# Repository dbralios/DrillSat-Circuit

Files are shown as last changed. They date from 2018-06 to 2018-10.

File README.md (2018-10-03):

# White Noise

[White Noise](fb.com/WhiteNoiseGRE) is a space-engineering team from the National Technical University of Athens and currently consists of 6 members ( in alphabetical order ) :

* Dimitris Bralios 
* Chariton Charitonidis
* Iasonas Nikolaou
* Spyros Pavlatos
* George Rapakoulias
* Miltiadis Stouras

Our team won 1st prize in the [CanSat in Greece 2018](cansat.gr) competition.

# DrillSat

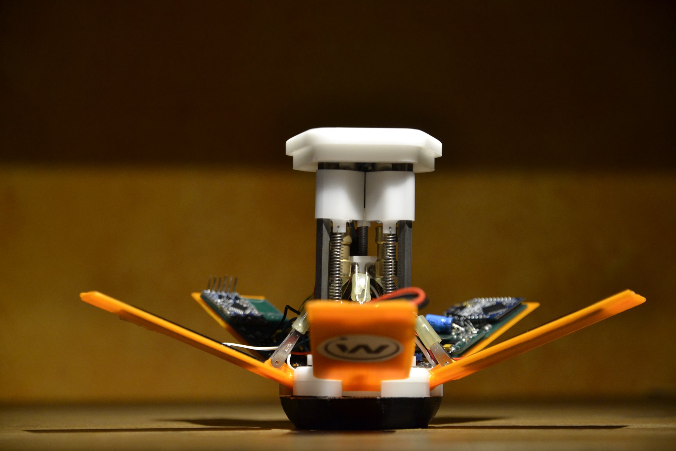
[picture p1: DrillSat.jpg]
DrillSat


Our goal was to develop a CanSat that can help in exploring new planets, as a part of our idea to use CubeSats in space exploration. Specifically, our CanSat, after a successful landing with the parachute, is able to use its [leg mechanism](https://www.youtube.com/watch?v=kTSUgSXn8OM) and rise into a position from which it can dig its drills to the ground and measure the soil's moisture with a sensor we developed.

# Electronics System 

The electronics system of the CanSat is comprised of an Arduino microcontroller, a UV sensor, a pressure and temperature sensor, a GPS, an XBee RF module, a conductivity sensor  and powered by a LiPo battery and four solar panels. The system apart from the battery the solar panels and the GPS, has to fit on top of two legs of the CanSat inside a space of 7x35x71mm. Due to that two PCBs were designed so the electronics can be mounted onto them. Also the structure has to be robust and survive any stresses, as well as operate continuously for 4 hours, constricting the power budget.

We have three boards on this repo. PCB1 connects an Arduino Pro Mini, an SD socket and a UV sensor (ML8511). PCB2 connects an XBee, the Solar Charger and a BMP sensor. The Solar Charger is a modified and shrunk version of the Adafruit board. 

PCB1 and PCB2 were designed on fritzing while the solar charger was designed on EAGLE.

## Sensor Subsystem

### Ultra Violet
The UV light sensor used is ML8511 mounted on a board. Equipped with an internal amplifier it converts the photo-diode current to voltage, outputing voltage linearly related to the UV light intensity measured in mW/cm2. The sensor output is stable across the operating temperature range, from -25C up to 75C, altough silght error is introduced away from the configuration temperature. Slight error is introduced by the temperature, although the operational temperature range is from -25C up to 75C. The spectral response is highest in the range 280 - 390nm which covers the UV-B spectrum and significant percentage of the UV-A spectrum. The typical supply current is around 300uA at the operational voltage of 3V.

### Pressure & Temperature
The sensor used to mesure temperature and barometric pressure is BMP280. The interface used to communicate with the microctroller is I2C. The pressure and temperature data, using the barometric formula, can give the current height with an accuracy of 1m. The operating pressure range is up to 9000m above sea level and from -40C to 85C regarding the temperature range, while the typical current draw is 2.7uA. 

### Conductivity Sensor

The conductivity sensor of the ground is implemented as a voltage divider. Two high speed steel drills are used space 18.2mm apart that penetrate 20mm in depth. One drill is connected to the ground voltage level while the other to +3.3V level through a 10KOhm resistor. Then the second drill is connected to an analogue pin of the microcontroller, as a result given the voltage at that pin and the resistance of the drills, we can specify the resistance between them.

### GPS

The GPS module used is the LEA-6H, which is mounted on the top of the CanSat. Typical supply current is 41mA and 47mA during the acquisition phase and the horizontal accuracy is 2.5m.

## Communication & Data Handling

### Microcontroller

The selected microcontroller board is the Arduino Pro Mini, using the ATmega328P, an 8-bit AVR microprocessor. It runs at 3.3V and 8MHz and has 14 input/output pins, 6 of them analog. The available program memory size is 32KByte, as well as 1024 Bytes of non volatile EEPROM memory, used to make the CanSat state-aware after possible power offs.

### RF Module

The RF module used for communication with the ground station is the XBee Pro S5 operating at 868MHz. It runs on 3.3 V consuming 60 mA at stand-by mode and 200 mA on packet emission and has a sensitivity of -112 dBm. It is used with an external antenna with 3 dBi gain. The same XBee module is also used on the ground station. The two modules are programmed to operate on AT Mode with ground station’s XBee being the coordinator and cansat’s XBee a router. Both modules transmit at a power of 25mW which is the legal local limit at 868MHz.

## Power Subsystem

A Polymer Lithium Ion battery, charged by four solar panels, is powering the CanSat. The battery has a voltage output of 3.7V and a capacity of 980mAh. Four 30.5mm by 58.5mm solar panels connected in serially, are used to charge the battery through the MCP73871. Then a low-dropout regulator drops the voltage down to 3.3V powering every piece of electronics, except for the GPS which has an onboard regulator and the the three motors.

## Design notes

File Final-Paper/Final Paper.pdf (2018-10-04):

## CFP-18-White-Noise

## CANSAT FINAL PAPER - DRILLSAT

### Authors Dimitris Bralios, bnbzor@gmail.com Chariton Charitonidis, haritoncharitonides@gmail.com Iasonas Nikolaou, iasonasnikolaou11@hotmail.com Spyros Pavlatos, spyrospavlatos4@gmail.com George Rapakoulias, george.rpk@outlook.com Miltiadis Stouras, m.stouras@gmail.com

Abstract: The CanSat in Greece competition aims at giving university students the opportunity to work on a multidisciplinary project with technology similar to that used in small satellites and to take their first steps in space. Moreover, the current trend in satellite technology which is to achieve more with a smaller probe, with prime examples being the CubeSats, makes this kind of competition more relevant. Our goal as a team was to design and build a CanSat that could be the basis for an actual space probe with the aim of extraterrestrial exploration. This paper presents our design of the CanSat discussing the mechanical, electrical and software aspects in detail, while showing that all the mission requirements are met. Specifically, our CanSat is launched onboard a research rocket and deployed at the apogee. Then a parachute is used to reach the nominal descent velocity. Equipped with five legs it is able to reach an upright position from where the drills can be activated. First, the leg and drill mechanisms are described in detail. Next, the selected sensors, the measurements taken and the electronics subsystem are discussed. Then, we present the flight software as well as the ground station that receives and visualizes the mission data in real time. Finally, we discuss the challenges we faced and draw conclusions.

CFP-18-White-Noise | Page 1 of 8

I. INTRODUCTION
The mission of our team for the 2018 CanSat in Greece competition consisted of the primary mission, same for all contestants, and the secondary one, selected by our team. In the primary mission we had to integrate sensors in our design, capable of measuring position, temperature and altitude during descent. The secondary mission was inspired from a number of real life projects in extraterrestrial exploration like the curiosity rover, the rosetta space probe, asteroid mining concepts etc. All those projects revolve around analysing the surface and soil of
planets | or | comets, | encountering | harsh
conditions. Our goal was to build a sensor for estimating soil moisture concentration and monitor it over time, in a supposed target planet, in order to further evaluate whether it could eventually host plants and support human activity. For further analysis, we added a UV sensor, since this is proven to be a key factor in the germination process.

II. PROJECT DESCRIPTION
The CanSat is launched onboard a Patriot type-rocket, with an apogee of 1 km where the probe is deployed. During the flight, a velocity of 500 km/h and an acceleration of 22 g could be reached. Next, throughout the descent the probe measures the barometric pressure, temperature and geographic coordinates. These measurements are stored as well as sent to the ground station in real time.
Requirements include the size of the probe, which has to fit inside a cylinder with a diameter of 65mm and a height of 115 mm. The descent rate after the deployment of the parachute should be in the range of 6 - 10 m/s. Also, the probe should be able to operate 4 hours continuously. Lastly, the mass of the CanSat should not exceed 350 grams.
Goal of the secondary mission is to measure the UV radiation and the soil moisture of the environment the CanSat is deployed in, from which we can exclude crucial information that can help us in our efforts to inhabit the target planet . After a successful landing with the parachute, it is able to use its leg mechanism and rise into a position from which it can dig its drills to the ground and measure the conductivity between the two drills, which is related to the moisture of the soil examined. Apart from the pressure and temperature sensor, a UV light sensor is added to determine if there is spectral content in the UV-A and UV-B range.
The data gathered are sent to the ground station, which is equipped with a high gain Yagi antenna with a range of 3 - 4 km. The frequency of the transmissions is 1 Hz. Through a web application the data received can be displayed and plotted in real time on a computer of the ground station.

III. MECHANICAL SYSTEM
In order to achieve our goals, a number of mechanisms had to be implemented in the design. The small size of the CanSat made it challenging to fit everything inside it in a robust way. After many prototypes, the following layout was chosen.

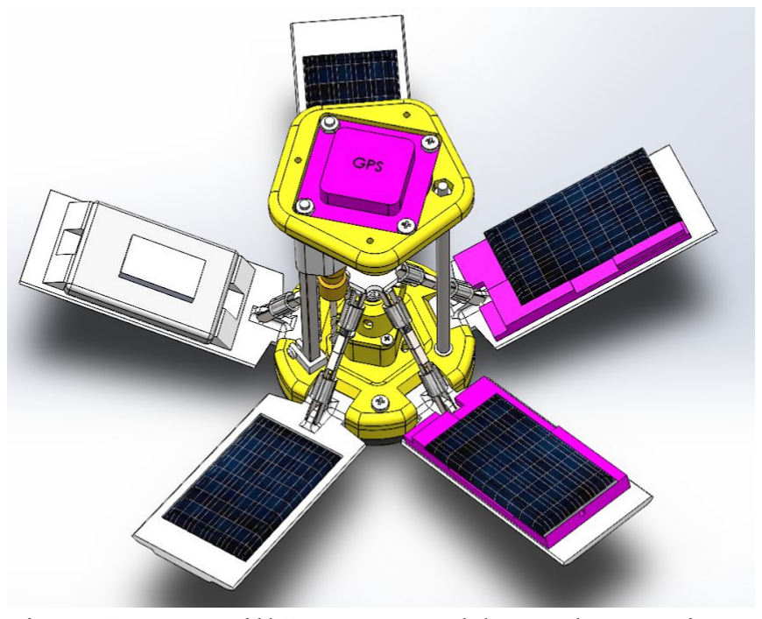
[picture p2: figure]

Fig. 1: DrillSat assembly, electronics represented with purple.

| All the electronics, the battery and the
solar panels were placed on the inside surface of the legs leaving space in the core of the CanSat for the drills and the leg deployment mechanism. A set of 5 foldable legs were placed in the periphery of the satellite, a number chosen to provide a good balance between leg width and near circular top view. A motor driven platform moving on a threaded rod, along with N clevis joints were used for deploying those legs. The length of each arm and the position of the joints were chosen carefully in order to give the mechanism an appropriate mechanical gain, allowing it to operate with a small motor and minimum current.

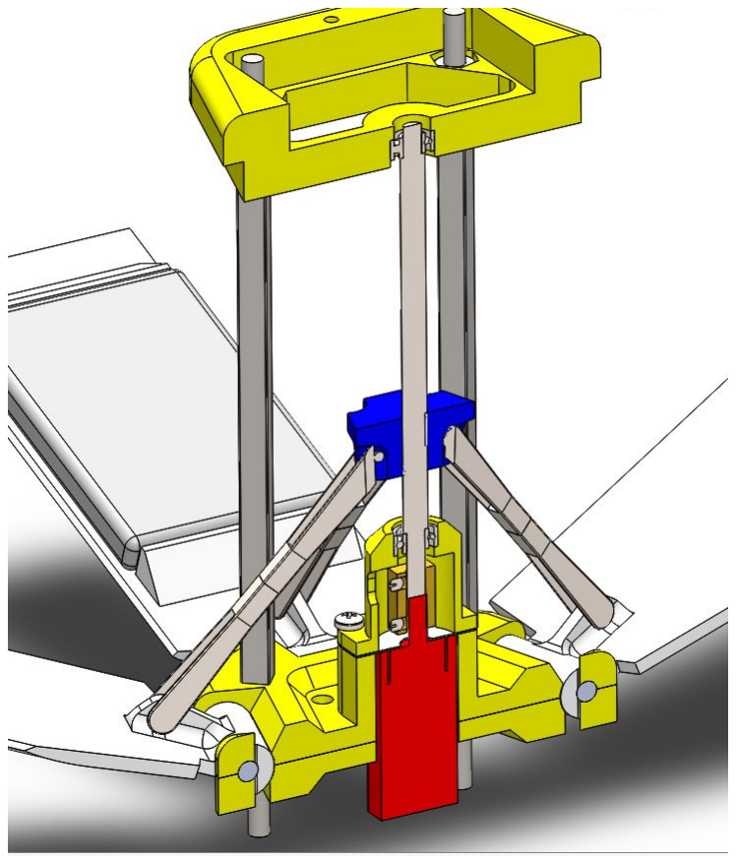
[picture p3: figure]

Fig. 2: Legs deployment mechanism

As for the drill mechanism, the drill assembly was sliding on a square 4x4 mm rod. In order to save space and weight, the assembly was moving with the aid of springs instead of actuators. An expendable retainer was used to prevent the drill from deploying. When voltage was applied to the motors, the drills would penetrate the retainer and protrude out of the CanSat, into the ground.

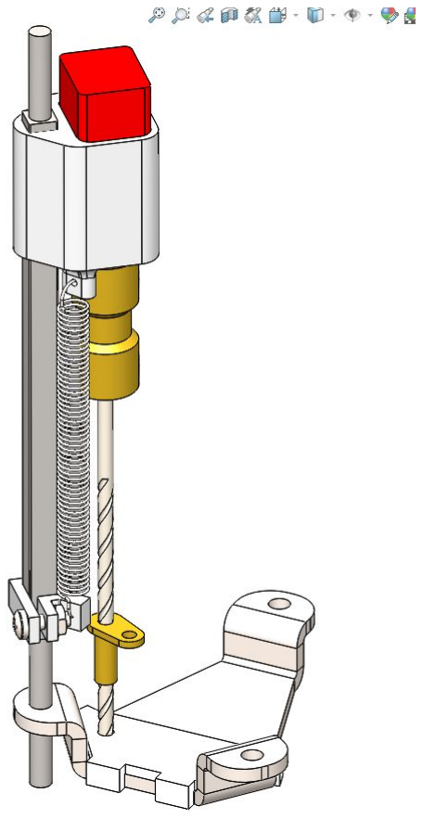
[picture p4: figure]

Fig. 3: Drill mechanism

Finally, in order to provide dampening in hard landings, some extra parts were added. A bottom made from TPC rubber was designed to make the first contact with the ground, absorbing most of the energy from the impact. Because the motor moving the legs was also located in the bottom of the satellite, we added a stainless steel metal cover around it.

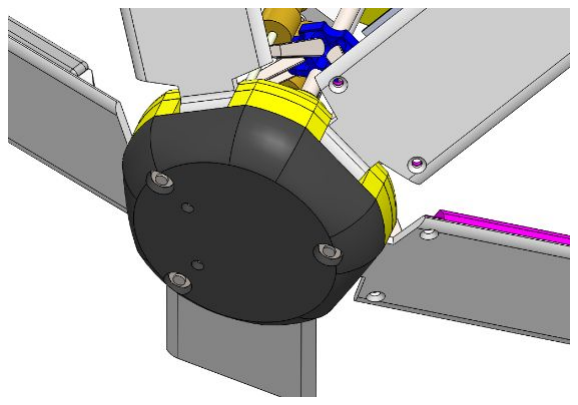
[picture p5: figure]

Fig. 4: Rubber damper

Most parts were CNC machined from POM plastic, ensuring high strength and dimensional precision. Metal parts were all made from stainless steel, with the exception of couplers, which were made from brass.
Apart from the satellite, we also constructed the parachute. We chose a classic circular design with a vent in the apex for stability. Its surface was first calculated theoretically using the following formula
F D = | [1]
2

CD

ρ V A

2

solved for A, given the terminal velocity (V), the total drag force (FD
), the air density (ρ) and the drag coefficient (CD

). After building the first prototype, fine-tuning was made in the surface area in order to achieve our target terminal velocity at 8 m/s, which we measured using image analysis from a video. Later on, for better precision, we also calculated the terminal velocity by conducting several drop tests in which we measured the height of the satellite in small constant time intervals and analyzed the measurements. The material we used was ripstop nylon. The diameter of the parachute was 48 cm and the diameter of the stability vent was 8 cm. A total of 8 buttonholes were made around the perimeter of the parachute fabric. A simple 2 mm kevlar thread was used for the suspension lines whose length was 50 cm enough to minimize the pitch of the CanSat.

IV. ELECTRONICS SYSTEM
The electronics system of the CanSat is comprised of an Arduino microcontroller, a UV sensor, a pressure and temperature sensor, a GPS, an XBee RF module anda conductivity sensor, all powered by a LiPo battery and four solar panels. The system apart from the battery the solar panels and the GPS, has to fit on top of two legs of the CanSat inside a space of 7x35x71 mm. Due to that two PCBs were designed so that the electronics can be mounted onto them. Also the structure had to be robust and survive any stresses, as well as being to run continuously for 4 hours, constricting the power budget.

IV.I. Sensor Subsystem
The UV light sensor used is ML8511 mounted on a board. Equipped with an internal amplifier it converts the photodiode current to voltage, outputting voltage linearly related to the UV light intensity measured in mW/cm

2
. The
sensor output is stable across the operating temperature range, from -25° C up to 75° C, although, when measuring in temperatures away from the one on which the sensor was calibrated, a slight error is introduced. The spectral response is highest in the range 280 - 390 nm which covers the UV-B spectrum and significant percentage of the UV-A spectrum. The typical supply current is around 300 μA at the operational voltage of 3 V.

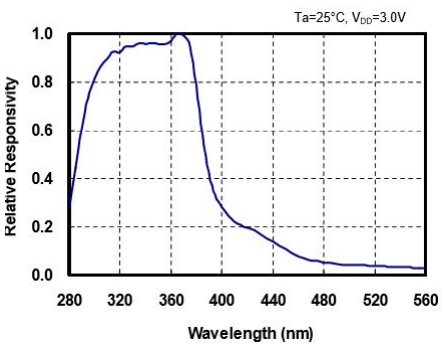
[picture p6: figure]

Fig. 5: Spectral response characteristics of ML8511

| The sensor used to measure temperature
and barometric pressure is BMP280. The interface used to communicate with the microcontroller is I2C. The pressure and temperature data, using the barometric formula, can give the current height with an accuracy of 1m. The operating pressure range is up to 9000 m above sea level and from -40° C to 85° C regarding the temperature range, while the typical current drawn is 2.7 μA.
The sensor used to measure the soil moisture is implemented as a voltage divider. Two high speed steel drills spaced 18.2mm apart are used to penetrate 20 mm in depth. One drill is connected to the ground voltage level through a 10K Ohm resistor while the other one to the +3.3 V level. The former drill is connected to an analog pin of the microcontroller. Given the voltage at that pin we can specify the resistance between them and then calculate the soil moisture.
The GPS module used is the LEA-6H, which is mounted on the top of the CanSat. It
sends | NAV-POSLLH | packages | to | the
microcontroller via serial connection, at a frequency of 1Hz. Typical supply current is 41 mA and 47 mA during the acquisition phase and the horizontal accuracy is 2.5 m.

IV.II. Communication and Data Handling The selected microcontroller board is the Arduino Pro Mini, using the ATmega328P, an 8-bit AVR microprocessor. It runs at 3.3 V and 8 MHz and has 14 input/output pins, 6 of them analog. The available program memory size is 32 KByte, as well as 1024 Bytes of non volatile EEPROM memory, used to make the CanSat state-aware after possible power offs. Apart from collecting and processing the measurements of the sensors the Arduino also controls the three motors through N-channel MOSFETS.
The RF module used for communication with the ground station is the XBee Pro S5 operating at 868MHz. It runs on 3.3 V consuming 60 mA at stand-by mode, 200 mA on packet emission and has a sensitivity of -112 dBm. It is used with an external antenna with 3 dBi gain which has the following radiation pattern.

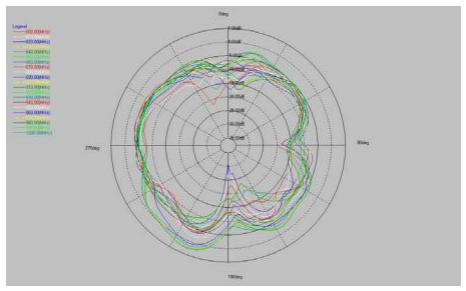
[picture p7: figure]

Fig. 6: Radiation pattern of the probe’s antenna

The same XBee module is also used on the ground station. The two modules are programmed to operate on AT Mode with ground station’s XBee being the coordinator and cansat’s XBee a router. Both modules transmit at a power of 25mW which is the legal local limit at 868MHz.

IV.III. Electrical Power Subsystem
A Polymer Lithium Ion battery, charged by four solar panels, is powering the CanSat. The battery has a voltage output of 3.7 V and a capacity of 980 mAh. Four 30.5 mm by 58.5 mm solar panels connected serially are used to charge the battery through the MCP73871. Then a low-dropout regulator drops the voltage down to 3.3 V powering every piece of electronics, except for the GPS, which has an onboard regulator, and the three motors.

Voltage
(V)

Current
(mA)

Power
(mW)
Arduino | 3.3 | 25 | 82.5
XBee | 3.3 | 60 | 198
GPS | 3.7 | 50 | 165
SD card | 3.3 | 30 | 99
BMP sensor 3.3 | 1 | 3.3
UV sensor | 3.3 | 0.5 | 1.65
Motors | 3.7 | 350 | 1295
Table 1: Power budget
Through experiments the previous values of current drawn were found. We conclude that the battery selected is able to power the CanSat for the required time duration.
V. FLIGHT SOFTWARE
The flight software consists of three software states: Launching, Descent and Ground Operations. In each state, the sequence of events is:
1. Take measurements
2. Save measurements to SD Card
3. Send a telemetry package containing the last measurements to ground station
4. Process data and determine the new software state

To ensure that our mission’s state is maintained through unexpected processor resets, some information regarding the current state is stored on the non-volatile memory (EEPROM) of the microcontroller, so it can be queried on processor start-up. Being able to dynamically determine our software state is vital for the success of the flight software because a simple sequential program could get stuck in the wrong software state after a sudden reset and lose control of the mission. The flight software is visualised in the flowchart of Fig. 7.

VI. GROUND CONTROL SYSTEM
The ground station consists of a personal computer, an Xbee Pro S5 and a Yagi Antenna with 8 dBi gain. The Xbee is connected via USB to the computer, and the Yagi Antenna is attached to the Xbee module with an RP-SMA connector. The data received by the computer, is parsed by a python script, checked for errors, and saved in a JSON format. Meanwhile a node.js server running locally serves a web page where the data is plotted in real-time using React.js and plotly.js.

VII. CONCLUSION
If we were to rebuild the satellite, we would have made a number of changes, both in the mechanisms and the circuits. One thing we found particularly hard was integrating all cables in the design. Lack of space along with the fact that the circuit boards were in moving parts of the cansat made this even harder. Using cable ribbons and socket connectors would give better results as well. Furthermore, a future upgrade would be the design of PCBs that host most of the electronics components, the sensors themselves and not serving as connectors between various sensor boards. Lastly, another minor enhancement would be to establish a 2-way communication with the satellite, changing the antennas’ and the software accordingly, in order to be able to query the satellite for values that are typically not included in mission’s telemetry packages (i.e. values stored in EEPROM), as well as have it to execute orders given from the ground station in real-time.
In conclusion, with the end of this project, our team has gained significant knowledge and experience. We believe that by constructing DrillSat we have proved our initial standing, that CanSats and CubeSats can include complex mechanisms and be used in a wide variety of space missions (such as extraterrestrial exploration) .

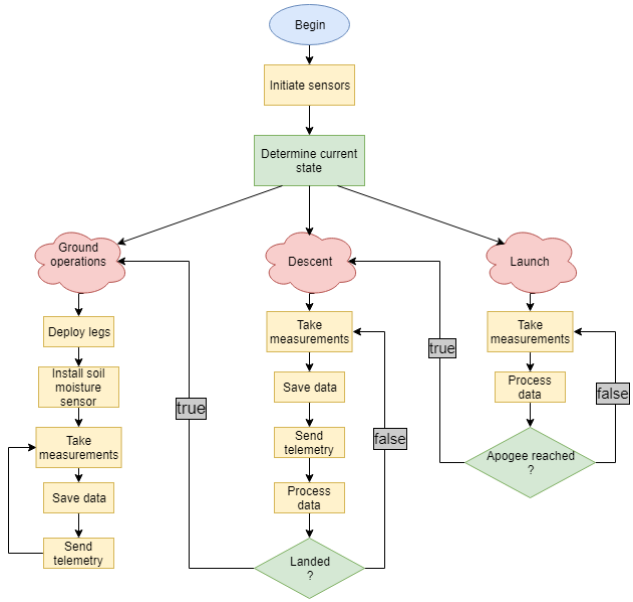
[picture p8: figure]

Fig. 7: Flight software flowchart

VII. REFERENCES
-CanSat in Greece portal: www.cansat.gr -Christos Papadopoulos, Machine Design, 3rd edition 2017
-UV Sensor with Voltage Output. ML8511. Rev. 5.0. Lapis Semiconductor. Mar. 2013.
-Digital Pressure Sensor. BMP280. Rev. 1.14. Bosch Sensortec. Mar. 2015.
-LEA-6 u-blox 6 GPS Modules. UBX-14044797. Rev. 13.0. U-blox. Feb. 2017.
-8-bit | AVR | Microcontrollers.
Atmel-42735B-ATmega328/P. Rev. B. Atmel. Nov. 2016.
-XBee-PRO 868 RF Module. Rev. F. Digi International. May. 2015.
-Polymer Lithium-Ion Battery. LP573450. Rev. 1.0. Cellevia Batteries. May. 2017.
-Stand-Alone | System | Load | Sharing | and
Li-Ion/Li-Polymer Battery Charge Management Controller. MCP73871. Rev. C. Microchip Technology. Sep. 2013.
-Arduino Documentation: www.arduino.cc

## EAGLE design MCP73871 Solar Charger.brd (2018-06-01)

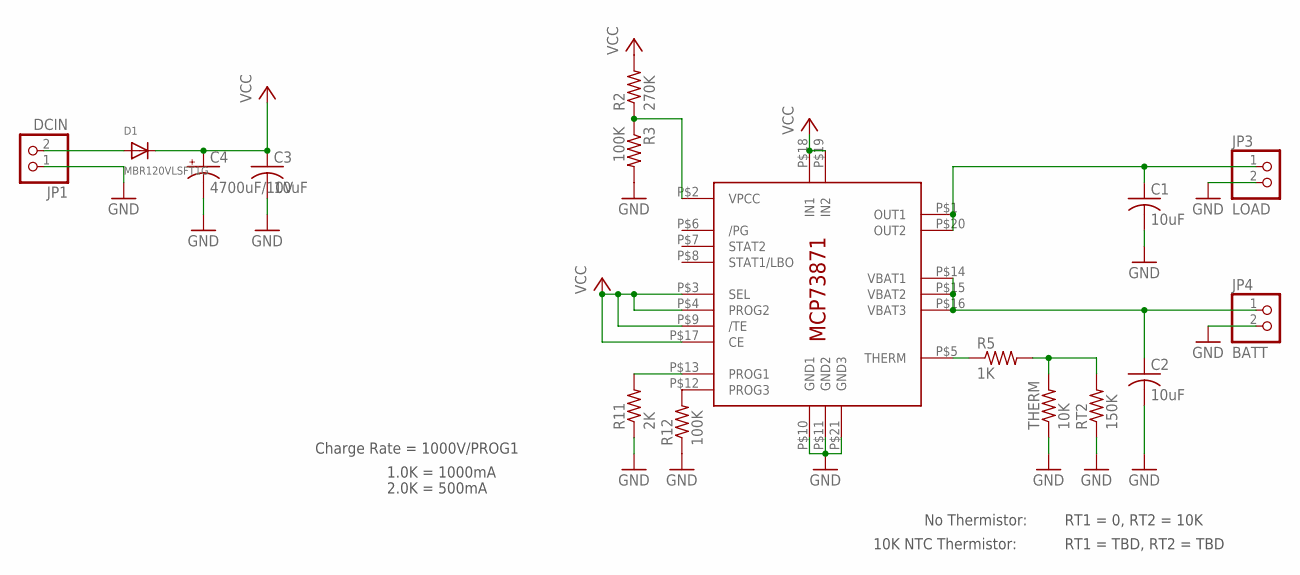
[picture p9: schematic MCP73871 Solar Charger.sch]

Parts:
C1, C2, C3: 10uF; C0805K
C4: 4700uF/10V; E5-10,5
D1: MBR120VLSFT1G; SOD-123
IC1: MCP73871; QFN20_4MM
JP1: DCIN; 1X02_OVAL
JP3: LOAD; 1X02_ROUND
JP4: BATT; 1X02_ROUND
R2: 270K; R0805
R3, R12: 100K; R0805
R5: 1K; M0805
R11: 2K; M0805
RT2: 150K; M0805
THERM: 10K; M0805

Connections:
BATT: C2.1, IC1.P$14 (VBAT1), IC1.P$15 (VBAT2), IC1.P$16 (VBAT3), JP4.1
GND: C1.2, C2.2, C3.2, C4.-, IC1.P$10 (GND1), IC1.P$11 (GND2), IC1.P$21 (GND3), JP1.1, JP3.2, JP4.2, R3.2, R11.1, R12.1, RT2.1, THERM.1
unnamed: D1.A, JP1.2
unnamed: IC1.P$5 (THERM), R5.1
unnamed: IC1.P$2 (VPCC), R2.1, R3.1
unnamed: R5.2, RT2.2, THERM.2
unnamed: IC1.P$12 (PROG3), R12.2
unnamed: IC1.P$13 (PROG1), R11.2
OUT: C1.1, IC1.P$1 (OUT1), IC1.P$20 (OUT2), JP3.1
VCC: C3.1, C4.+, D1.C, IC1.P$3 (SEL), IC1.P$4 (PROG2), IC1.P$9 (/TE), IC1.P$17 (CE), IC1.P$18 (IN1), IC1.P$19 (IN2), R2.2

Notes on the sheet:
Charge Rate = 1000V/PROG1
1.0K = 1000mA
2.0K = 500mA
No Thermistor:
10K NTC Thermistor:
RT1 = 0, RT2 = 10K
RT1 = TBD, RT2 = TBD

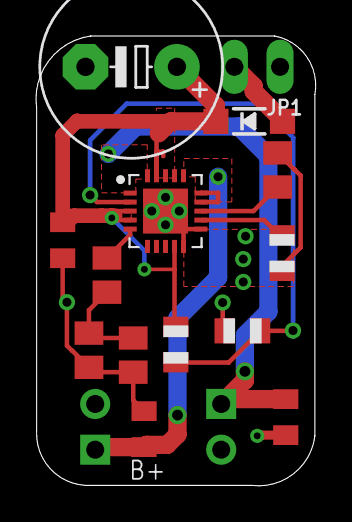
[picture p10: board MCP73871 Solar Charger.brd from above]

Board: 2 copper layers, 15.5 x 25.0 mm, 16 parts (0 on the bottom side), 10 nets.
